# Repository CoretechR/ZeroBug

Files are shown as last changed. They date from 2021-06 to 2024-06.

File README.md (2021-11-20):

# ZeroBug - DIY Hexapod Robot

Zerobug is a 3D-printed micro-servo hexapod robot powered by a Raspberry Pi Zero and a STM32F103. The Pi Zero is in charge of the input methods and front end, making the robot controllable via mouse, keyboard, multitouch or simply a Bluetooth Gamepad. To get the robot walking, the STM32 handles leg locomotion, inverse kinematics and controls its 18 servos.

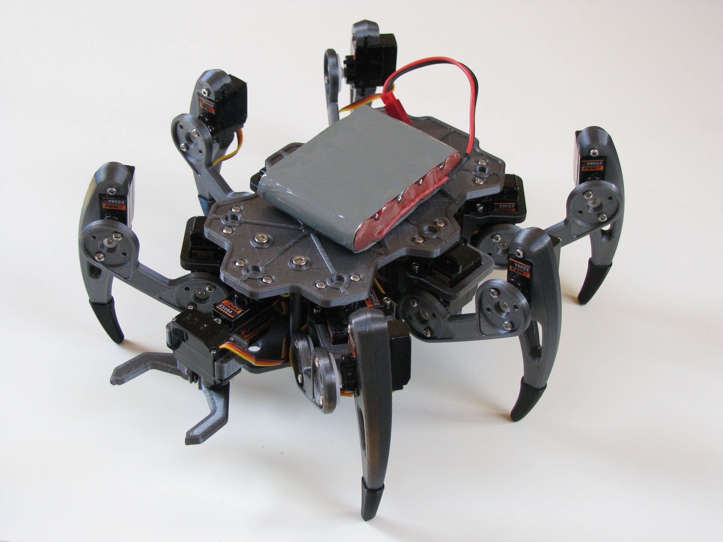
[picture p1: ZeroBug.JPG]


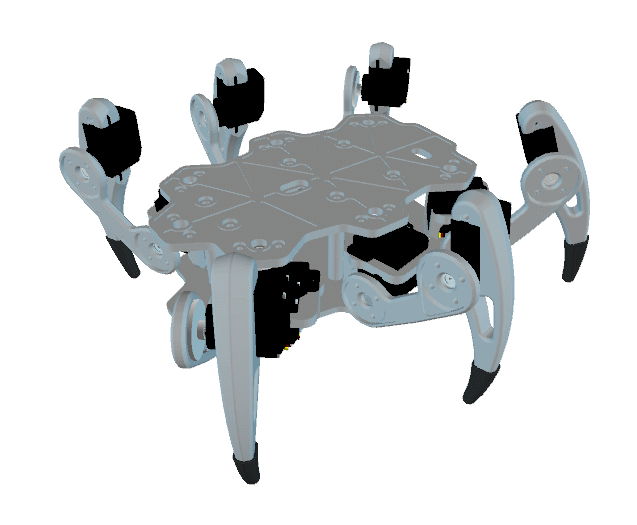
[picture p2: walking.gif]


UPDATE 20.11.2021: Added support for video streaming with via the camera connector:
 - update the index-html file and copy "start_stream.sh" to the same directory on the desktop
 - install mjpg-streamer (e.g. using this guide: https://www.okdo.com/project/pc-webcam-with-raspberry-pi/?ok_ts=1635608250445)
 - add the following line to the /etc/rc.local file (before exit 0):
```
bash /home/pi/Desktop/hexapod/start_stream.sh
```

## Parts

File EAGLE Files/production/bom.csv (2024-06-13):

Designator | Footprint | Quantity | Value | LCSC Part #
@HOLE0, @HOLE1, @HOLE10, @HOLE11, @HOLE12, @HOLE13, @HOLE2, @HOLE3, @HOLE4, @HOLE5, @HOLE6, @HOLE7, @HOLE8, @HOLE9 |  | 14
C1 | 0805 | 1 | 10uF
C10, C11, C14, C15, C2, C8 | 0805 | 6 | 1.0uF
C12, C13 | 0603 | 2 | 47pF
C17 | 0603 | 1 | 10nF
C18, C9 | 0805 | 2 | 2.2uF
C20, C21 | 0603 | 2 | 0.1uF
C3 | 0805 | 1 | 4.7uF
C5 | PANASONIC_D | 1 | 100uF
C6, C7 | 0603 | 2 | 18pF
CN1 | 1X04-BIG | 1 | 1X4-BIG
D1, D3 | SOD-323 | 2 | BAT20J
D2 | LED-0603@2 | 1 | BLUE
F1 | PTC-1206 | 1 | 500mA
J1 | TERMBLOCK_1X2-3.5MM | 1
J10, J11, J12, J13, J14, J15, J16, J17, J18, J19, J20, J21, J22, J3, J4, J5, J6, J7, J8, J9 | 1X03 | 20
J2 | USB-C-16P | 1
J23 | 61031021821 | 1
OSC0 | CRYSTAL-SMD-5X3 | 1 | 8MHz
Q1 | TO252 | 1 | AOD417
R1, R2 | 0603 | 2 | 0
R12, R15, R4, R6, R7, R8 | 0603 | 6 | 10k
R13, R14 | 0603 | 2 | 27
R16, R17, R18, R9 | 0603 | 4 | 1k
R19, R3 | 0603 | 2 | 5.1k
R20 | 0603 | 1 | 1k5
R5 | 0603 | 1 | 4.7k
S1 | TACTILE_SWITCH_SMD_4.6X2.8MM | 1 | RESET
SJ1, SJ2 | PAD-JUMPER-2-NO_YES_SILK | 2
U$2 | QFN-24-4MM2 | 1 | MPU-6050-1
U2 | TSSOP28 | 1
U3 | SOT23-5 | 1 | AP2112K-3.3V
U4 | SOT230P700X180-4N | 1 | MCP1825S-5002E/DB
UC1 | LQFP48 | 1 | STM32F103CBT6

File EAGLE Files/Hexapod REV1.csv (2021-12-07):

Qty | Value | Device | Package | Parts | Description | DATASHEET-URL | GENDER | IR | MPN | OC_FARNELL | OC_NEWARK | PACKAGE | PACKAGING | PART-NUMBER | PINS | PROD_ID | ROWS | SUPPLIER | TYPE | VALUE | WE-NUMBER
1 |  | 6103XX21821_61031021821 | 61031021821 | J23 | WR-PHD 2.54 mm SMT Dual Socket Header (Reel) | https://katalog.we-online.com/em/datasheet/61031021821.pdf | Socket Header | 3A |  |  |  |  | Tape and Reel with Cap | 61031021821 | 10 |  | Dual |  | Straight Type 2 |  | 61031021821
20 |  | CONN_03 | 1X03 | J3; J4; J5; J6; J7; J8; J9; J10; J11; J12; J13; J14; J15; J16; J17; J18; J19; J20; J21; J22 | Multi connection point. Often used as Generic Header-pin footprint for 0.1 inch spaced/style header connections |  |  |  |  |  |  |  |  |  |  | XXX-00000 |  |  |  | 455-1750-1-ND
2 |  | JUMPER-PAD-2-NOYES_SILK | PAD-JUMPER-2-NO_YES_SILK | SJ1; SJ2
1 |  | PCA9685 | TSSOP28 | U2 | PCA9685 - 16 Channel 12-Bit I2C PWM Controller
1 |  | TERMBLOCK_1X2 | TERMBLOCK_1X2-3.5MM | J1 | 3.5mm Terminal block
1 |  | USB_C16PIN | USB-C-16P | J2 | USB Type C 16Pin Connector |  |  |  |  |  |  |  |  |  |  | CONN-14122
2 | 0 | 10KOHM-0603-1/10W-1% | 0603 | R1; R2 | 10kO resistor |  |  |  |  |  |  |  |  |  |  | RES-00824 |  |  |  | 10k
2 | 0.1uF | 0.1UF-0603-25V-(+80/-20%) | 0603 | C20; C21 | 0.1µF ceramic capacitors |  |  |  |  |  |  |  |  |  |  | CAP-00810 |  |  |  | 0.1uF
6 | 1.0uF | 1.0UF-0805-25V-(+80/-20%) | 0805 | C2; C8; C10; C11; C14; C15 | 1µF ceramic capacitors |  |  |  |  |  |  |  |  |  |  | CAP-11625 |  |  |  | 1.0uF
1 | 100uF | 100UF-POLAR-25V-20%(ELEC) | PANASONIC_D | C5 | 100µF polarized capacitors |  |  |  |  |  |  |  |  |  |  | CAP-12547 |  |  |  | 100uF
6 | 10k | 10KOHM-0603-1/10W-1% | 0603 | R4; R6; R7; R8; R12; R15 | 10kO resistor |  |  |  |  |  |  |  |  |  |  | RES-00824 |  |  |  | 10k
1 | 10nF | 47PF-0603-50V-5% | 0603 | C17 | 47pF ceramic capacitors |  |  |  |  |  |  |  |  |  |  | CAP-08913 |  |  |  | 47pF
1 | 10uF | 1.0UF-0805-25V-(+80/-20%) | 0805 | C1 | 1µF ceramic capacitors |  |  |  |  |  |  |  |  |  |  | CAP-11625 |  |  |  | 1.0uF
2 | 18pF | 47PF-0603-50V-5% | 0603 | C6; C7 | 47pF ceramic capacitors |  |  |  |  |  |  |  |  |  |  | CAP-08913 |  |  |  | 47pF
1 | 1X4-BIG | 1X4-BIG | 1X04-BIG | CN1 | 4-pin connector
3 | 1k | 10KOHM-0603-1/10W-1% | 0603 | R16; R17; R18 | 10kO resistor |  |  |  |  |  |  |  |  |  |  | RES-00824 |  |  |  | 10k
1 | 1k | 1KOHM-0603-1/10W-1% | 0603 | R9 | 1kO resistor |  |  |  |  |  |  |  |  |  |  | RES-07856 |  |  |  | 1k
1 | 1k5 | 10KOHM-0603-1/10W-1% | 0603 | R20 | 10kO resistor |  |  |  |  |  |  |  |  |  |  | RES-00824 |  |  |  | 10k
2 | 2.2uF | 1.0UF-0805-25V-(+80/-20%) | 0805 | C9; C18 | 1µF ceramic capacitors |  |  |  |  |  |  |  |  |  |  | CAP-11625 |  |  |  | 1.0uF
2 | 27 | 27OHM1/10W1%(0603)0603-RES | 0603 | R13; R14 | RES-09334 |  |  |  |  |  |  |  |  |  |  | RES-09334
1 | 4.7k | 10KOHM-0603-1/10W-1% | 0603 | R5 | 10kO resistor |  |  |  |  |  |  |  |  |  |  | RES-00824 |  |  |  | 10k
1 | 4.7uF | 1.0UF-0805-25V-(+80/-20%) | 0805 | C3 | 1µF ceramic capacitors |  |  |  |  |  |  |  |  |  |  | CAP-11625 |  |  |  | 1.0uF
2 | 47pF | 47PF-0603-50V-5% | 0603 | C12; C13 | 47pF ceramic capacitors |  |  |  |  |  |  |  |  |  |  | CAP-08913 |  |  |  | 47pF
2 | 5.1k | 10KOHM-0603-1/10W-1% | 0603 | R3; R19 | 10kO resistor |  |  |  |  |  |  |  |  |  |  | RES-00824 |  |  |  | 10k
1 | 500mA | PTCSMD | PTC-1206 | F1 | Resettable Fuse PTC |  |  |  |  |  |  |  |  |  |  | RES-11150
1 | 8MHz | CRYSTAL5X3 | CRYSTAL-SMD-5X3 | OSC | Crystals
1 | AOD417 | MOSFET-PTO252 | TO252 | Q1 | P-Channel Mosfet
1 | AP2112K-3.3V | V_REG_LDOSMD | SOT23-5 | U3 | Voltage Regulator LDO |  |  |  |  |  |  |  |  |  |  | VREG-12457
2 | BAT20J | DIODE-SCHOTTKY-BAT20J | SOD-323 | D1; D3 | Schottky diodes in SFE's production catalog |  |  |  |  |  |  |  |  |  |  | DIO-11623 |  |  |  | BAT20J
1 | BLUE | LED-BLUE0603 | LED-0603@2 | D2 | Blue SMD LED |  |  |  |  |  |  |  |  |  |  | DIO-08575 |  |  |  | BLUE
1 | MCP1825S-5002E/DB | MCP1825S-5002E/DB | SOT230P700X180-4N | U4 | IC; LDO; 5.0V; 500MA |  |  |  | MCP1825S-5002E/DB | 1578407 | 26M9964 | SOT-223-3 |  |  |  |  |  | Microchip
1 | MPU-6050-1 | MPU-6050-1 | QFN-24-4MM2 | U$2
1 | RESET | MOMENTARY-SWITCH-SPST-2-SMD-4.6X2.8MM | TACTILE_SWITCH_SMD_4.6X2.8MM | S1 | Momentary Switch (Pushbutton) - SPST - Two Circuits |  |  |  |  |  |  |  |  |  |  | SWCH-13065
1 | STM32F103CBT6 | STM32F103CB | LQFP48 | UC1

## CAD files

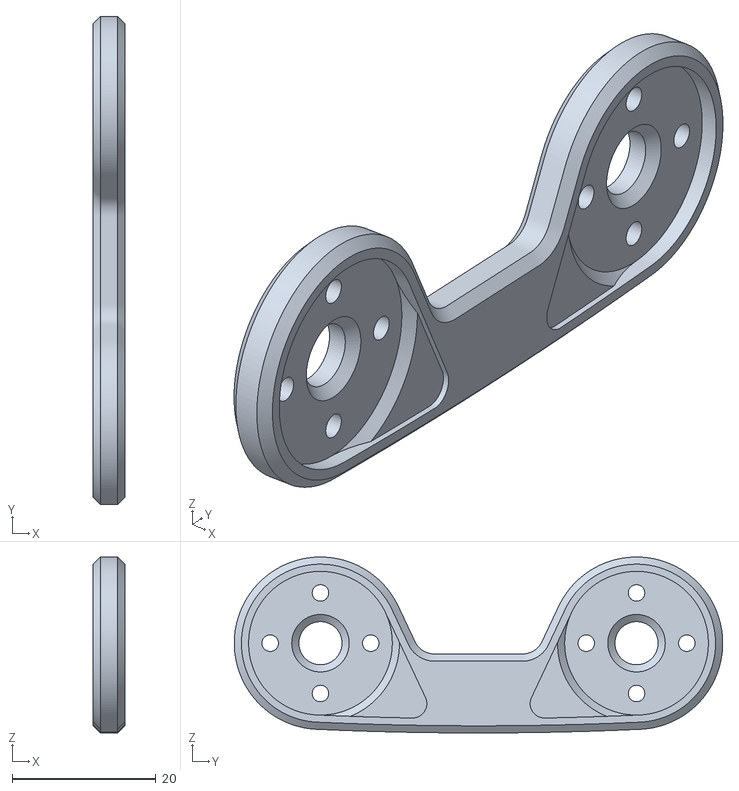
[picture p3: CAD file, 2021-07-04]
CAD Files/femur.stl
4.40 x 68.0 x 24.5

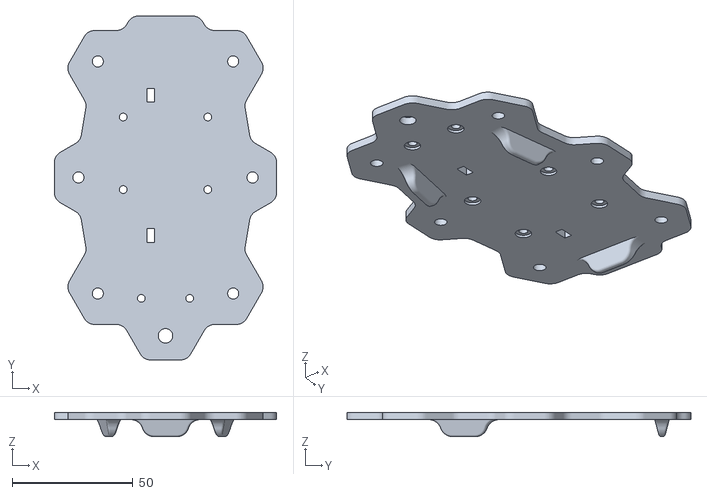
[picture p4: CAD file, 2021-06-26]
CAD Files/Body Bot.stl
92.0 x 142.3 x 10.0

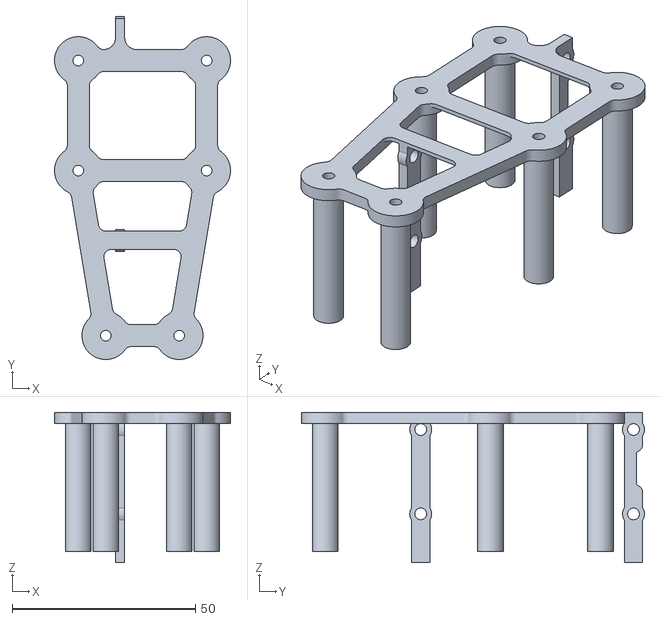
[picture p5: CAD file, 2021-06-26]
CAD Files/Spacer.stl
48.0 x 93.5 x 41.0

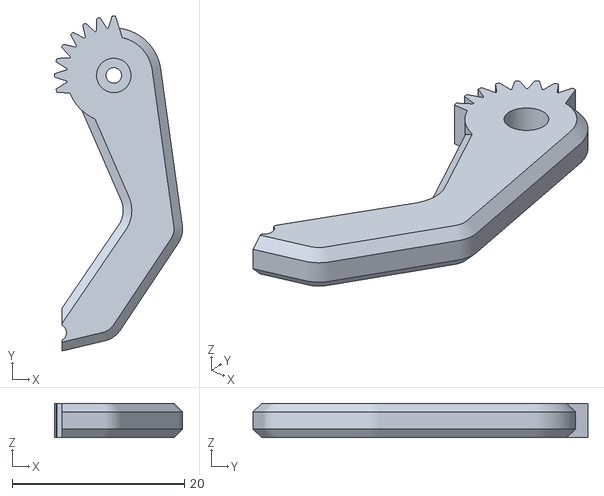
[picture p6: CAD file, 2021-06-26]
CAD Files/gripper_clawL.stl
14.9 x 38.9 x 4.00

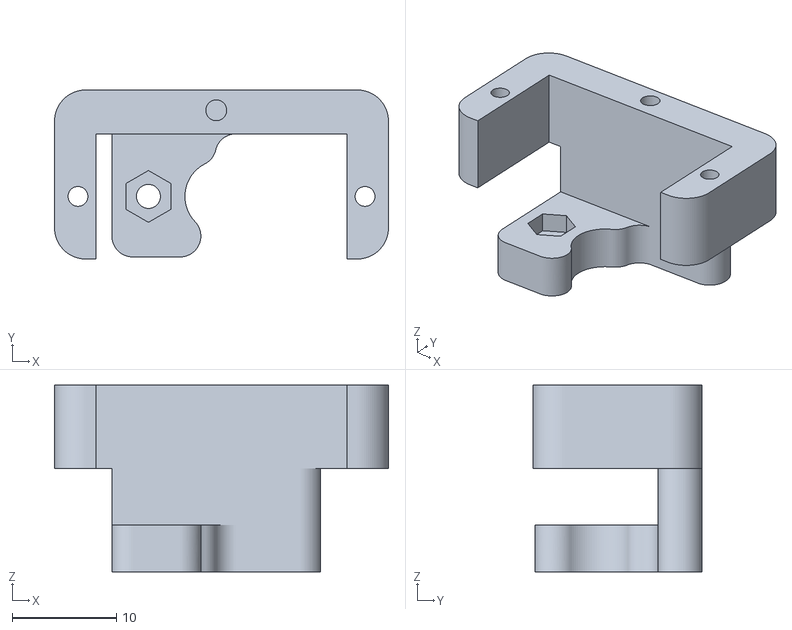
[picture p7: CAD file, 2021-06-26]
CAD Files/gripper_body.stl
32.0 x 16.2 x 17.9

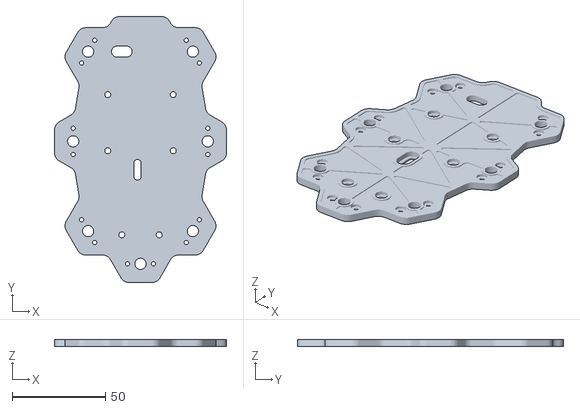
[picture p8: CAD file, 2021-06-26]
CAD Files/Body Top.stl
92.0 x 142.3 x 3.60

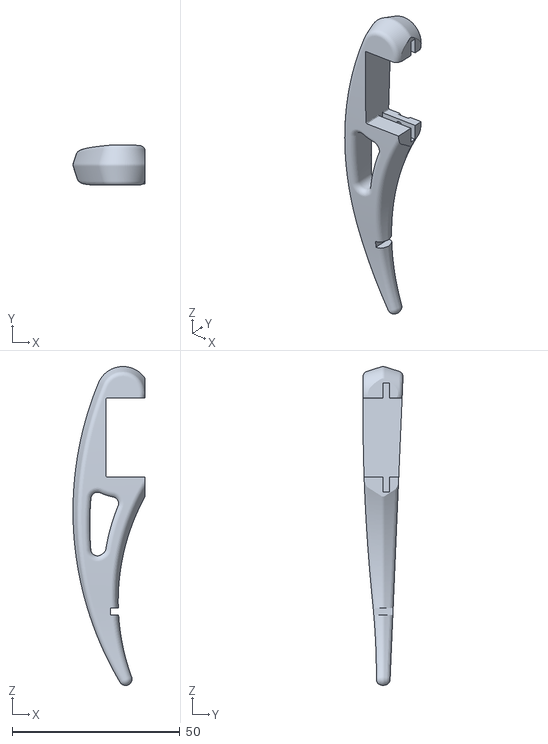
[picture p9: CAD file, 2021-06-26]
CAD Files/Tibia.stl
21.5 x 11.9 x 95.1

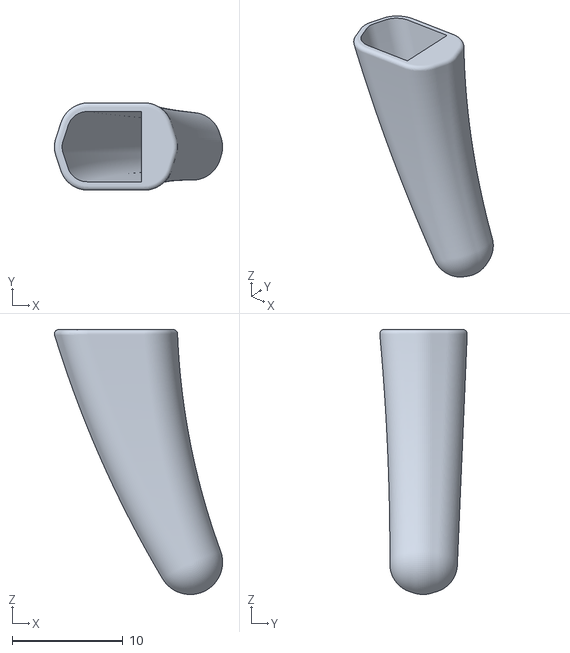
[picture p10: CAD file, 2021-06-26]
CAD Files/Sock.stl
15.2 x 7.89 x 23.9

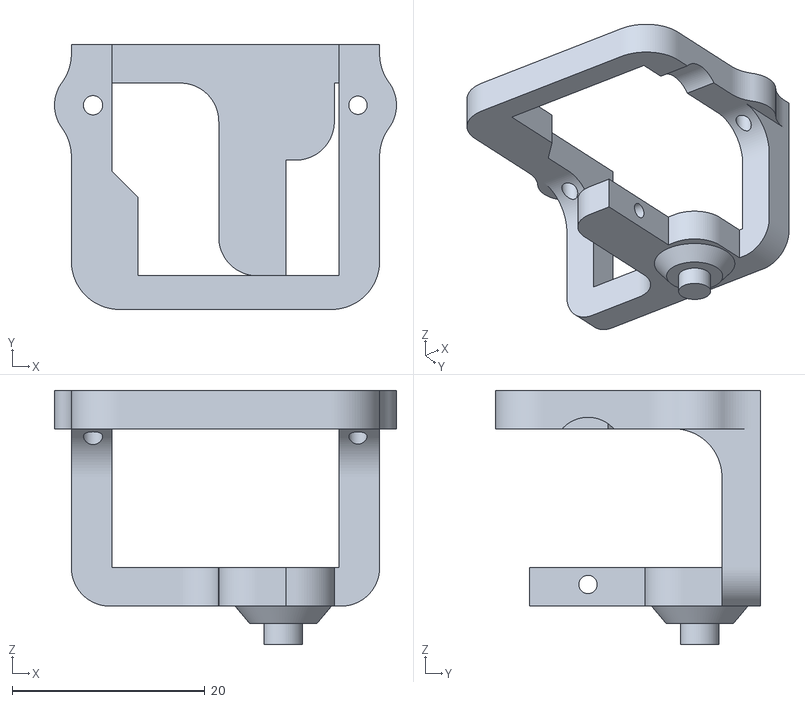
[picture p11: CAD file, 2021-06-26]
CAD Files/Coxa.stl
35.5 x 27.5 x 26.4

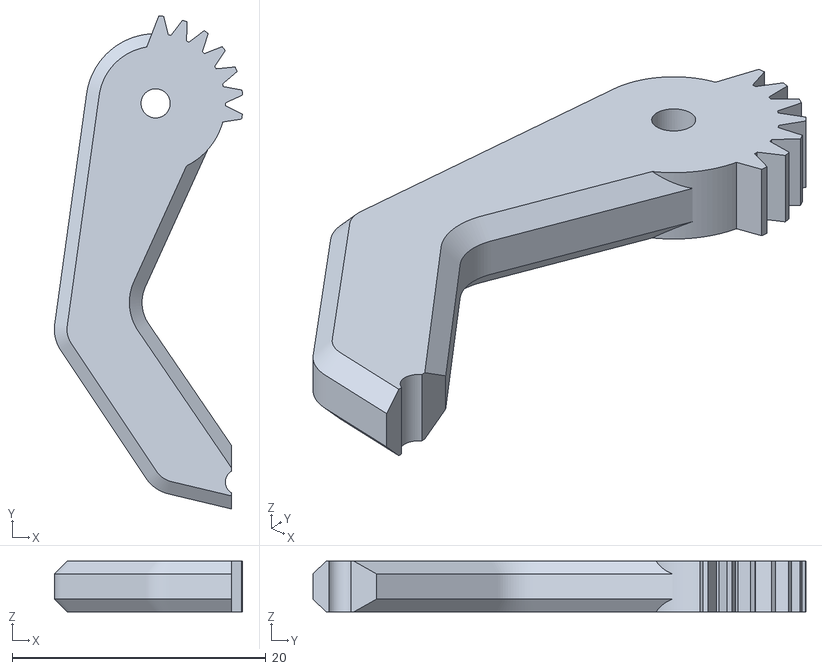
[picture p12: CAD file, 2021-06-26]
CAD Files/gripper_clawR.stl
14.9 x 38.9 x 4.00

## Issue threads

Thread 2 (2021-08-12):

miss file for CAD File

nongxiaoming, 2021-08-12:
hi，also miss some file for CAD File. no have the CoxaM.stl and TibiaM.stl??

CoretechR, 2021-08-12:
Hi, those are just the mirrored variants. Your slicer software should have an option to flip the parts. If not I can upload them as well.

nongxiaoming, 2021-08-19:
Ok,Got it.Thanks

Closed 2021-08-19.

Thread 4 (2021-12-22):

Raspberry PI software does not work

kenking2536, 2021-12-22:
Raspberry PI software does not work

I'm not familiar with Raspberry PI. Please guide me how to install it,

Copy what files to where??

What documents and contents are modified??

I'm using Raspberry PI zero 2 W

Not Raspberry PI zero w

kenking2536, 2021-12-25:
After many days of hard work! Learned a lot of knowledge! Finally, this problem occurs! Please have a look!
My zero 2 W installation process is as follows:

sudo apt-get install subversion
sudo apt-get install imagemagick
sudo apt-get install cmake
sudo apt-get install git
sudo apt-get install libv4l-dev
sudo apt-get install libopencv-dev
sudo apt-get install gcc g++
sudo apt-get install libjpeg9-dev
sudo apt-get install libjpeg62-turbo-dev
sudo apt-get install xrdp
sudo apt-get install samba
sudo apt-get install nodejs
sudo apt-get install npm
npm install socket.io
pip3 install aiohttp
pip3 install aiodns
pip3 install cchardet
pip3 install asyncio
pip3 install pygame
sudo git clone https://github.com/jacksonliam/mjpg-streamer
cd mjpg-streamer/mjpg-streamer-experimental
sudo make all
sudo make install
/home/pi/mjpg-streamer/mjpg-streamer-experimental/./mjpg_streamer -i "input_raspicam.so -x 1280 -y 720 -fps 12" -o "output_http.so -w ./www"
sudo cp mjpg_streamer@.service /etc/systemd/system
cd /etc/systemd/system
sudo mv mjpg_streamer@.service mjpg_streamer.service
sudo nano /etc/systemd/system/mjpg_streamer.service
sudo systemctl start mjpg_streamer.service
sudo systemctl enable mjpg_streamer.service
vcgencmd get_camera

Finally, the following error is displayed:
Traceback (most recent call last):
  File "/home/pi/ZeroBug/app.py", line 2, in <module>
    import socketio
ModuleNotFoundError: No module named 'socketio'

Closed 2021-12-25.

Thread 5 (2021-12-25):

Raspberry PI software does not work

kenking2536, 2021-12-25:
Raspberry PI software does not work

I'm not familiar with Raspberry PI. Please guide me how to install it,

Copy what files to where??

What documents and contents are modified??

I'm using Raspberry PI zero 2 W

Not Raspberry PI zero w

After many days of hard work! Learned a lot of knowledge! Finally, this problem occurs! Please have a look!
My zero 2 W installation process is as follows:

sudo apt-get install subversion
sudo apt-get install imagemagick
sudo apt-get install cmake
sudo apt-get install git
sudo apt-get install libv4l-dev
sudo apt-get install libopencv-dev
sudo apt-get install gcc g++
sudo apt-get install libjpeg9-dev
sudo apt-get install libjpeg62-turbo-dev
sudo apt-get install xrdp
sudo apt-get install samba
sudo apt-get install nodejs
sudo apt-get install npm
npm install socket.io
pip3 install aiohttp
pip3 install aiodns
pip3 install cchardet
pip3 install asyncio
pip3 install pygame
sudo git clone https://github.com/jacksonliam/mjpg-streamer
cd mjpg-streamer/mjpg-streamer-experimental
sudo make all
sudo make install
/home/pi/mjpg-streamer/mjpg-streamer-experimental/./mjpg_streamer -i "input_raspicam.so -x 1280 -y 720 -fps 12" -o "output_http.so -w ./www"
sudo cp mjpg_streamer@.service /etc/systemd/system
cd /etc/systemd/system
sudo mv mjpg_streamer@.service mjpg_streamer.service
sudo nano /etc/systemd/system/mjpg_streamer.service
sudo systemctl start mjpg_streamer.service
sudo systemctl enable mjpg_streamer.service
vcgencmd get_camera

Finally, the following error is displayed:
Traceback (most recent call last):
File "/home/pi/ZeroBug/app.py", line 2, in
import socketio
ModuleNotFoundError: No module named 'socketio'

pageauc, 2021-12-25:
You might try

sudo apt install socket.io

rather than rpm install

On Fri, Dec 24, 2021 at 8:41 PM kenking2536 ***@***.***>
wrote:

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

--
YouTube Channel at https://www.youtube.com/user/pageaucp
<http://www.youtube.com/user/pageaucp>
GitHub Repository at https://github.com/pageauc

kenking2536, 2021-12-25:
socket. IO problem solved!

thank!

Universal sudo apt-get install

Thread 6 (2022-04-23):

STM32F103C8T6

debian-user-france1, 2022-04-23:
The STM32F103C8T6 is not available anymore, what can I buy instead without reprogramming or much trouble?

debian-user-france1, 2022-04-23:
EMAX ES08A II Micro Servos are sold out, too

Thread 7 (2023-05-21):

Is the mpu 6050 used?

renhang123, 2023-05-21:
Hi, I looked at your source code and I can't seem to find the code for reading mpu 6050 data. Could you tell me where the data of mpu 6050 is used?

CoretechR, 2023-05-21:
Hi, the MPU6050 was never used on this board. I was planning to use it for balancing and still has some room on the PCB but never got around to implement it.

Closed 2023-05-22.

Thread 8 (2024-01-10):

Programming the STM32

weizhuowang, 2024-01-10:
Thanks for open sourcing the project! I see that the STM32F103 is using Arduino code. I wonder what is the best way to send the bootloader to mcu so that it accepts flashes from USB port?

CoretechR, 2024-01-10:
Hi, I wrote some instruction for another project that uses the STM32F103: https://github.com/CoretechR/Keybon
Maybe this will help you already.

Closed 2024-01-10.

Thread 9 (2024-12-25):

Servo Motor Replacement: EMAX ES08A II vs. Tower Pro MG90S

BiyolojiMeb, 2024-12-25:
Hello,
I can't find the EMAX ES08A II servo motor. Would it be okay if I use the Tower Pro MG90S instead?
Thanks!

CoretechR, 2024-12-25:
Hi, you should be able to use any micro servo, but you have to check the exact dimensions. The 3D-printed parts and especially the screw holes will probably not fit without some modifications.
Generally, I would recommend using the ES08A or a higher quality servo. The MG90S are not as fast and precise as the ES08A.

tianyi725, 2024-12-28:
> Hi, you should be able to use any micro servo, but you have to check the exact dimensions. The 3D-printed parts and especially the screw holes will probably not fit without some modifications. Generally, I would recommend using the ES08A or a higher quality servo. The MG90S are not as fast and precise as the ES08A.

thankyou

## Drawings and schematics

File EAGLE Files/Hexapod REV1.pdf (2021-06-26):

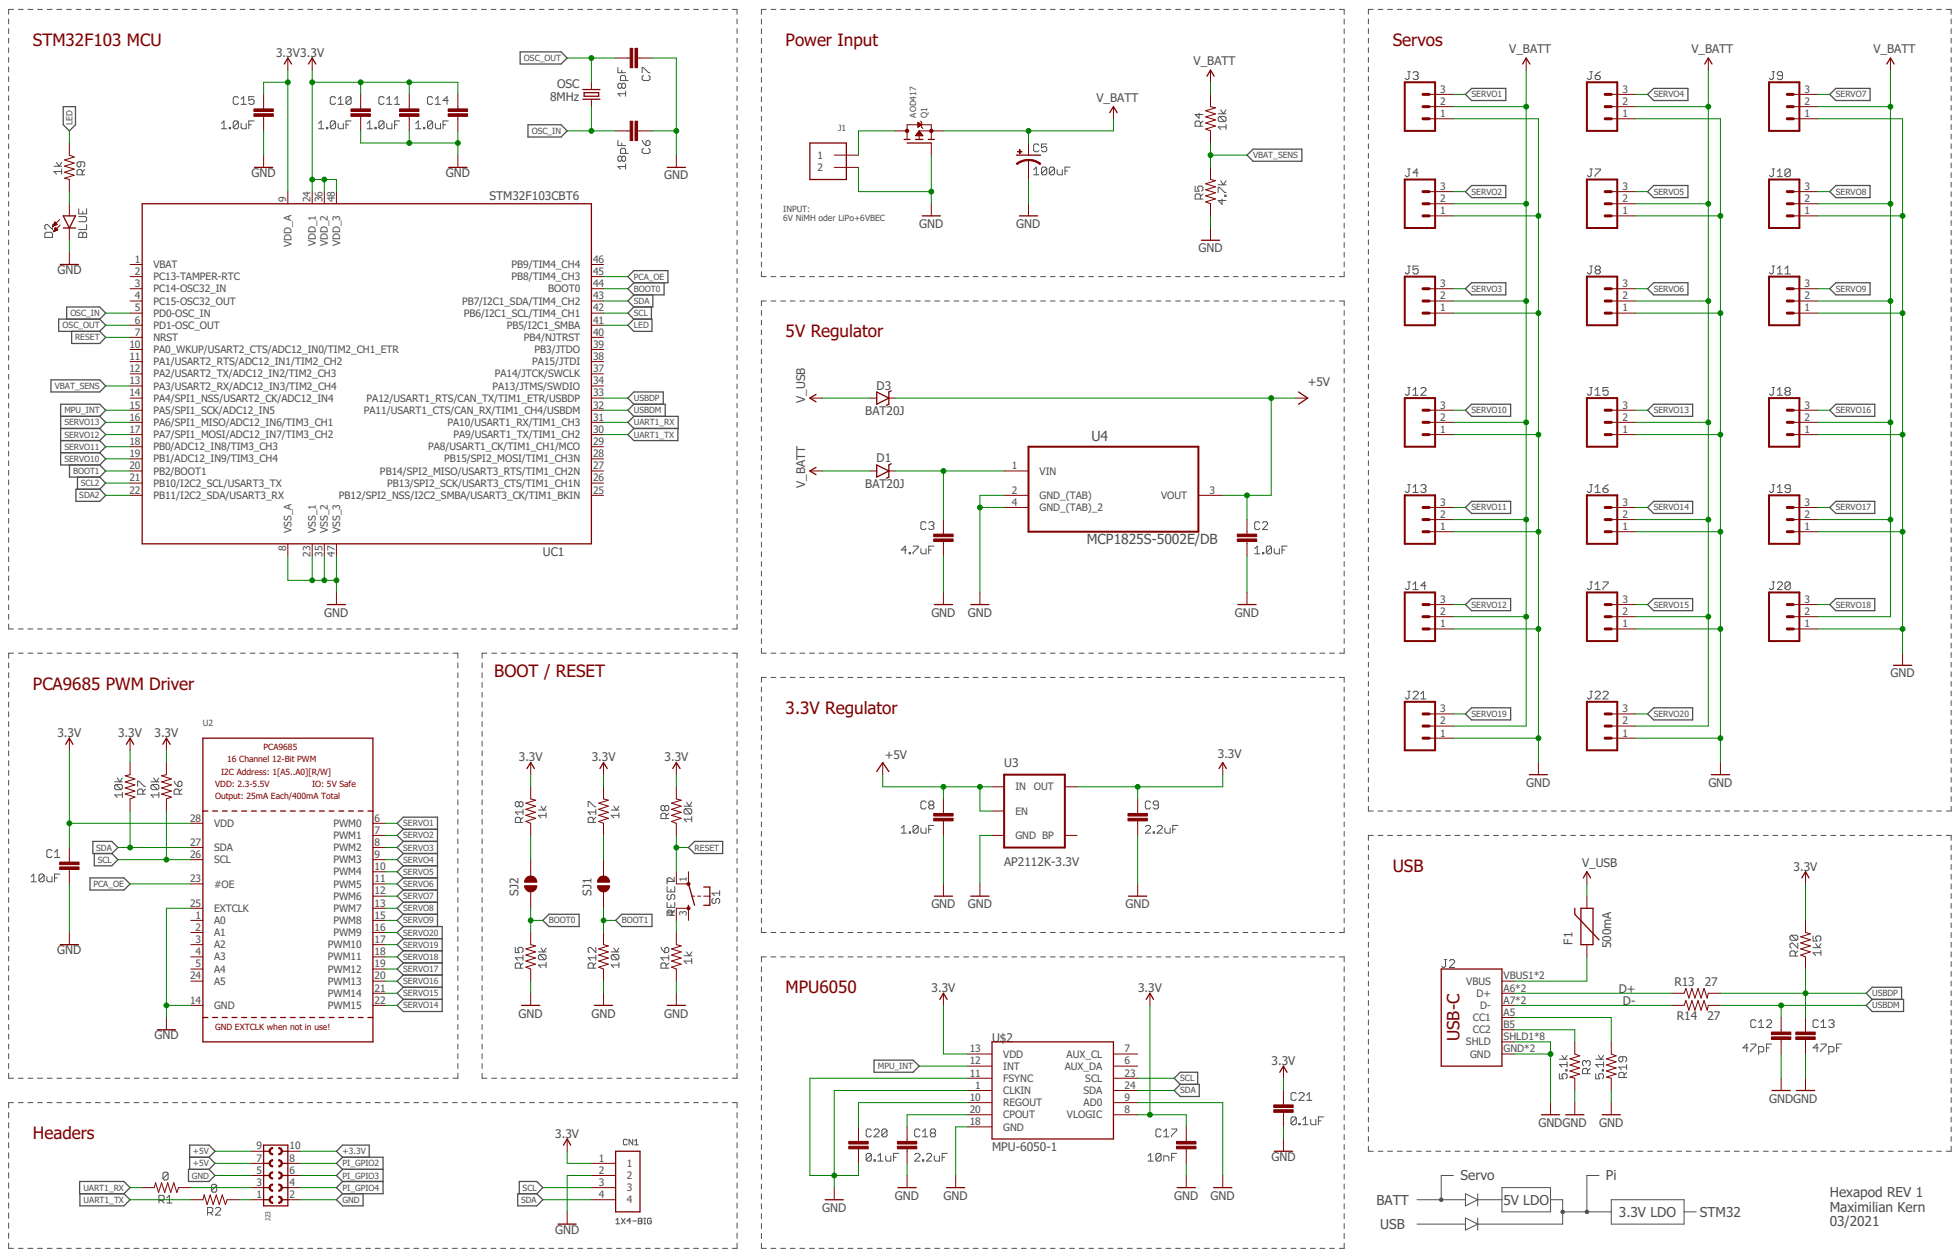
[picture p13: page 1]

INPUT: 6V NiMH oder LiPo+6VBEC

GND EXTCLK when not in use!

Hexapod REV 1 Maximilian Kern

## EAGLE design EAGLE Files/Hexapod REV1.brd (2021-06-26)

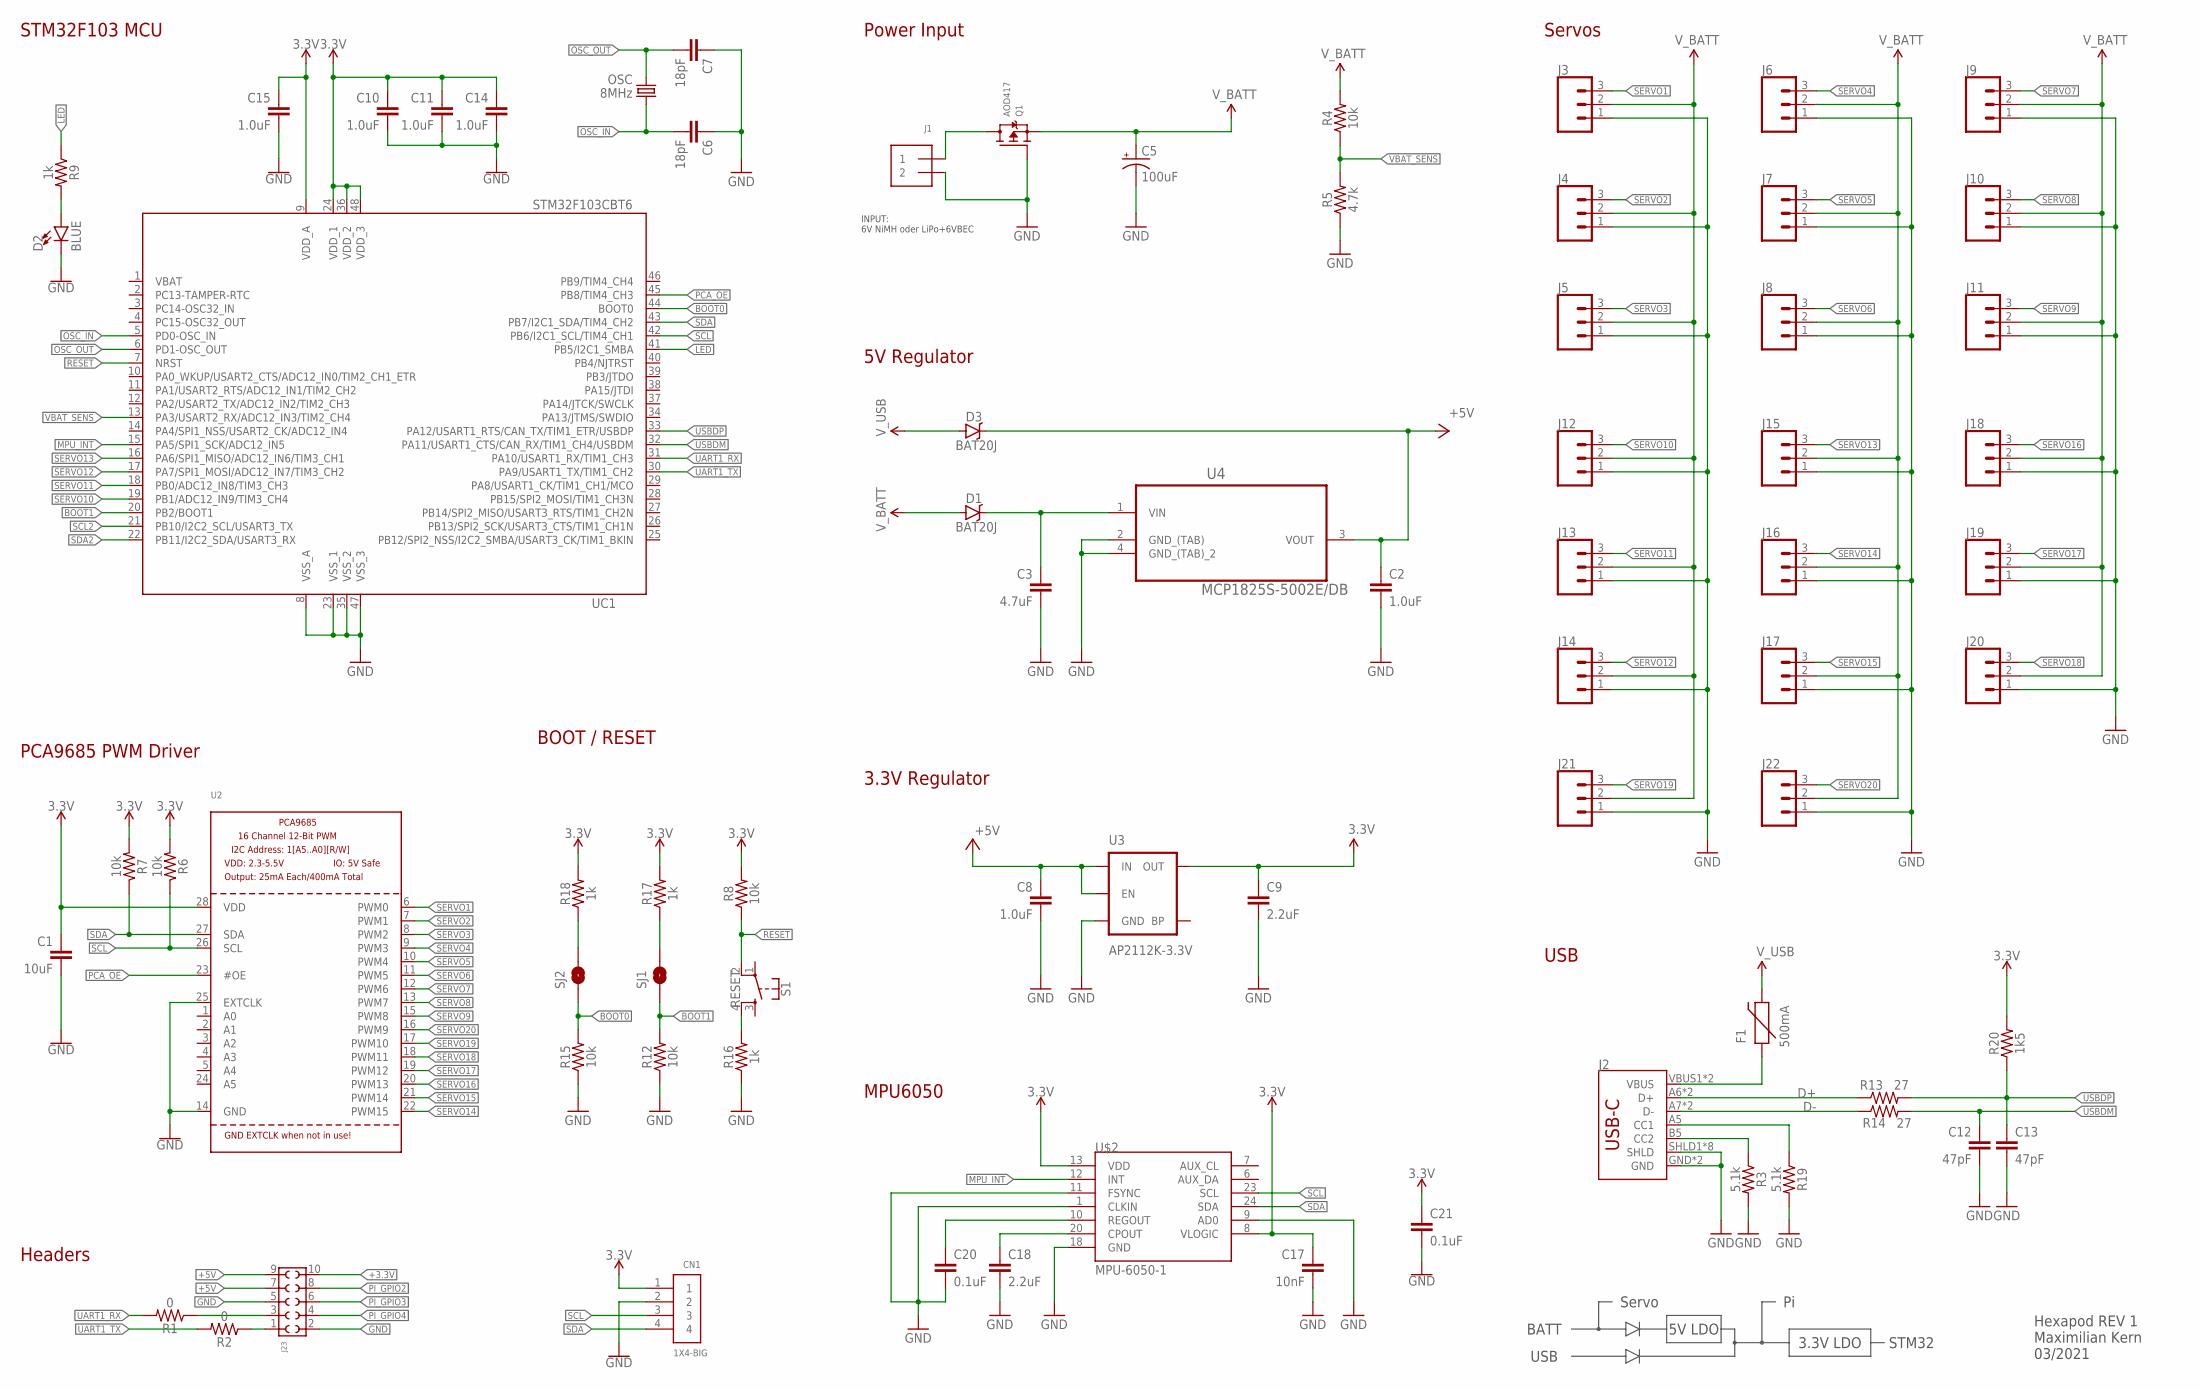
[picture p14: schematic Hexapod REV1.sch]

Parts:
C1: 10uF; 0805
C2, C8, C10, C11, C14, C15: 1.0uF; 0805
C3: 4.7uF; 0805
C5: 100uF; PANASONIC_D
C6, C7: 18pF; 0603
C9, C18: 2.2uF; 0805
C12, C13: 47pF; 0603
C17: 10nF; 0603
C20, C21: 0.1uF; 0603
CN1: 1X4-BIG; 1X04-BIG
D1, D3: BAT20J; SOD-323
D2: BLUE; LED-0603@2
F1: 500mA; PTC-1206
J1: TERMBLOCK_1X2; TERMBLOCK_1X2-3.5MM
J2: USB_C16PIN; USB-C-16P
J3, J4, J5, J6, J7, J8, J9, J10, J11, J12, J13, J14, J15, J16, J17, J18, J19, J20, J21, J22: CONN_03; 1X03
J23: 6103XX21821_61031021821; 61031021821
OSC: 8MHz; CRYSTAL-SMD-5X3
Q1: AOD417; TO252
R1, R2: 0; 0603
R3, R19: 5.1k; 0603
R4, R6, R7, R8, R12, R15: 10k; 0603
R5: 4.7k; 0603
R9, R16, R17, R18: 1k; 0603
R13, R14: 27; 0603
R20: 1k5; 0603
S1: RESET; TACTILE_SWITCH_SMD_4.6X2.8MM
SJ1, SJ2: JUMPER-PAD-2-NOYES_SILK; PAD-JUMPER-2-NO_YES_SILK
U2: PCA9685; TSSOP28
U3: AP2112K-3.3V; SOT23-5
U4: MCP1825S-5002E/DB; SOT230P700X180-4N
U$2: MPU-6050-1; QFN-24-4MM2
UC1: STM32F103CBT6; LQFP48

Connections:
3.3V: C1.1, C9.1, C10.1, C11.1, C14.1, C15.1, C17.1, C21.1, CN1.1, R6.2, R7.2, R8.2, R17.2, R18.2, R20.2, U2.28 (VDD), U3.5 (OUT), U$2.8 (VLOGIC), U$2.13 (VDD), UC1.9 (VDD_A), UC1.24 (VDD_1), UC1.36 (VDD_2), UC1.48 (VDD_3)
+3.3V: J23.10
+5V: C2.1, C8.1, D3.C, J23.7, J23.9, U3.1 (IN), U3.3 (EN), U4.3 (VOUT)
BOOT0: R15.2, SJ2.1, UC1.44 (BOOT0)
BOOT1: R12.2, SJ1.1, UC1.20 (PB2/BOOT1)
D+: J2.A6 (D+), J2.B6 (D+), R13.1
D-: J2.A7 (D-), J2.B7 (D-), R14.1
GND: C1.2, C2.2, C3.2, C5.-, C6.1, C7.1, C8.2, C9.2, C10.2, C11.2, C12.2, C13.2, C14.2, C15.2, C17.2, C18.2, C20.2, C21.2, CN1.2, D2.C, J1.2, J2.GND, J2.GND2 (GND), J2.SHLD1 (SHLD), J2.SHLD2 (SHLD), J2.SHLD3 (SHLD), J2.SHLD4 (SHLD), J2.SHLD5 (SHLD), J2.SHLD6 (SHLD), J2.SHLD7 (SHLD), J2.SHLD8 (SHLD), J3.1, J4.1, J5.1, J6.1, J7.1, J8.1, J9.1, J10.1, J11.1, J12.1, J13.1, J14.1, J15.1, J16.1, J17.1, J18.1, J19.1, J20.1, J21.1, J22.1, J23.2, J23.5, Q1.1 (G), R3.2, R5.1, R12.1, R15.1, R16.1, R19.2, U2.14 (GND), U2.25 (EXTCLK), U3.2 (GND), U4.2 (GND_(TAB)), U4.4 (GND_(TAB)_2), U$2.1 (CLKIN), U$2.9 (AD0), U$2.11 (FSYNC), U$2.18 (GND), UC1.8 (VSS_A), UC1.23 (VSS_1), UC1.35 (VSS_2), UC1.47 (VSS_3)
LED: R9.1, UC1.41 (PB5/I2C1_SMBA)
MPU_INT: U$2.12 (INT), UC1.15 (PA5/SPI1_SCK/ADC12_IN5)
unnamed: R16.2, S1.4
unnamed: R18.1, SJ2.2
unnamed: R17.1, SJ1.2
unnamed: C3.1, D1.C, U4.1 (VIN)
unnamed: D2.A, R9.2
unnamed: J1.1, Q1.3 (D)
unnamed: J2.A5 (CC1), R19.1
unnamed: J2.B5 (CC2), R3.1
unnamed: C18.1, U$2.20 (CPOUT)
unnamed: C20.1, U$2.10 (REGOUT)
OSC_IN: C6.2, OSC.1, UC1.5 (PD0-OSC_IN)
OSC_OUT: C7.2, OSC.3 (2), UC1.6 (PD1-OSC_OUT)
PCA_OE: U2.23 (#OE), UC1.45 (PB8/TIM4_CH3)
PI_GPIO2: J23.8
PI_GPIO3: J23.6
PI_GPIO4: J23.4
PI_RXD: J23.1, R2.1
PI_TXD: J23.3, R1.1
RESET: R8.1, S1.2, UC1.7 (NRST)
SCL: CN1.3, R6.1, U2.26 (SCL), U$2.23 (SCL), UC1.42 (PB6/I2C1_SCL/TIM4_CH1)
SCL2: UC1.21 (PB10/I2C2_SCL/USART3_TX)
SDA: CN1.4, R7.1, U2.27 (SDA), U$2.24 (SDA), UC1.43 (PB7/I2C1_SDA/TIM4_CH2)
SDA2: UC1.22 (PB11/I2C2_SDA/USART3_RX)
SERVO1: J3.3, U2.6 (PWM0)
SERVO2: J4.3, U2.7 (PWM1)
SERVO3: J5.3, U2.8 (PWM2)
SERVO4: J6.3, U2.9 (PWM3)
SERVO5: J7.3, U2.10 (PWM4)
SERVO6: J8.3, U2.11 (PWM5)
SERVO7: J9.3, U2.12 (PWM6)
SERVO8: J10.3, U2.13 (PWM7)
SERVO9: J11.3, U2.15 (PWM8)
SERVO10: J12.3, UC1.19 (PB1/ADC12_IN9/TIM3_CH4)
SERVO11: J13.3, UC1.18 (PB0/ADC12_IN8/TIM3_CH3)
SERVO12: J14.3, UC1.17 (PA7/SPI1_MOSI/ADC12_IN7/TIM3_CH2)
SERVO13: J15.3, UC1.16 (PA6/SPI1_MISO/ADC12_IN6/TIM3_CH1)
SERVO14: J16.3, U2.22 (PWM15)
SERVO15: J17.3, U2.21 (PWM14)
SERVO16: J18.3, U2.20 (PWM13)
SERVO17: J19.3, U2.19 (PWM12)
SERVO18: J20.3, U2.18 (PWM11)
SERVO19: J21.3, U2.17 (PWM10)
SERVO20: J22.3, U2.16 (PWM9)
UART1_RX: R1.2, UC1.31 (PA10/USART1_RX/TIM1_CH3)
UART1_TX: R2.2, UC1.30 (PA9/USART1_TX/TIM1_CH2)
USBDM: C12.1, R14.2, UC1.32 (PA11/USART1_CTS/CAN_RX/TIM1_CH4/USBDM)
USBDP: C13.1, R13.2, R20.1, UC1.33 (PA12/USART1_RTS/CAN_TX/TIM1_ETR/USBDP)
VBAT: UC1.1 (VBAT)
VBAT_SENS: R4.1, R5.2, UC1.13 (PA3/USART2_RX/ADC12_IN3/TIM2_CH4)
VUSB-RAW: F1.1, J2.VBUS1 (VBUS), J2.VBUS2 (VBUS)
V_BATT: C5.+, D1.A, J3.2, J4.2, J5.2, J6.2, J7.2, J8.2, J9.2, J10.2, J11.2, J12.2, J13.2, J14.2, J15.2, J16.2, J17.2, J18.2, J19.2, J20.2, J21.2, J22.2, Q1.2 (S), R4.2
V_USB: D3.A, F1.2

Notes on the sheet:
STM32F103 MCU
USB
BOOT / RESET
3.3V Regulator
Hexapod REV 1 Maximilian Kern 03/2021
INPUT: 6V NiMH oder LiPo+6VBEC
5V LDO
3.3V LDO
Servo
BATT
STM32
MPU6050
Power Input
Servos
PCA9685 PWM Driver
Headers
5V Regulator

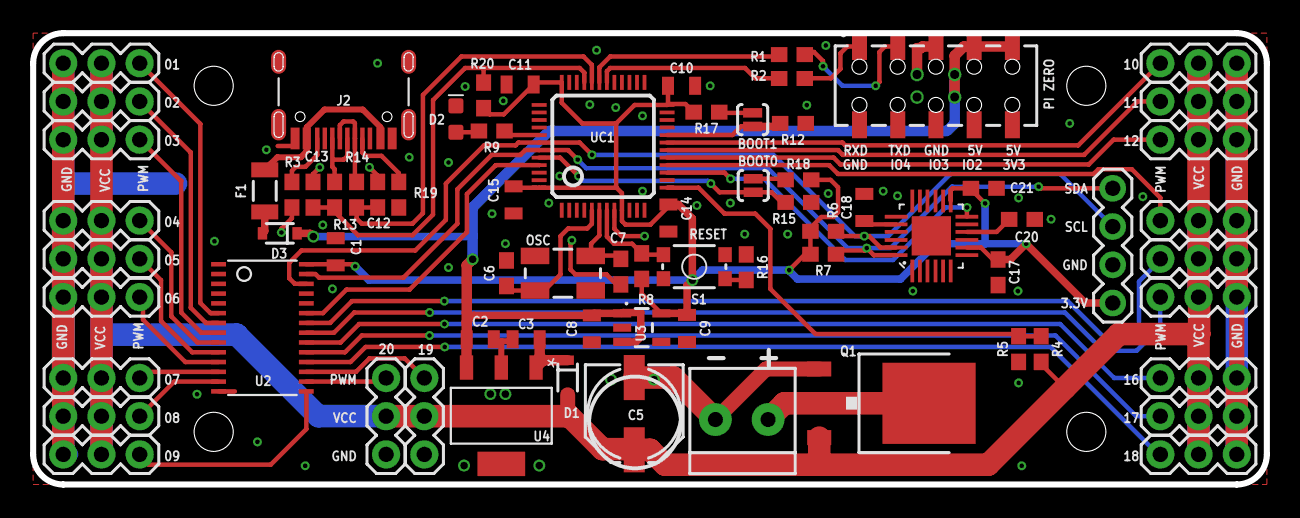
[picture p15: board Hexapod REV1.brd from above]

Board: 2 copper layers, 82.0 x 30.0 mm, 74 parts (0 on the bottom side), 55 nets.

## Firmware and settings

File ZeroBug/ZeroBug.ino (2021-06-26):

#include "ZeroBug.h"

#include <Adafruit_PWMServoDriver.h>
#include <Servo.h>

#define LED PB5
#define SDA1 PB7
#define SCL1 PB6
#define PCA_OE PB8

Adafruit_PWMServoDriver pwm = Adafruit_PWMServoDriver(0x40, Wire);

#define SERVOMIN  604.0 // This is the 'minimum' pulse length count (out of 4096)
#define SERVOMAX  2260.0 // This is the 'maximum' pulse length count (out of 4096)
#define SERVO_FREQ 50 // Analog servos run at ~50 Hz updates

Servo servo[4]; // local pwm servos

gaitEngine Hex;

byte tripodGait[120][6];
byte waveGait[120][6];

float jX = 0; // (Joystick) Walking X, Y and Rotate
float jY = 0.0;
float jR = 0.0;

long frameCounter = 0;

char inputBuffer[64]; // = "m 123.123 000.456 789.001";

float vBat = 0;

boolean IKError = false;

boolean powerup = false;
boolean powerdown = false;

boolean clawOpen = false;
boolean clawClose = false;
float clawPos = 0;

long controlTimeout;

void setup() {

  pinMode(LED, OUTPUT);
  pinMode(PCA_OE, OUTPUT);  
  digitalWrite(PCA_OE, HIGH);
  
  // tripod gait
  Hex.gaitSpeed = 1.0;
  Hex.legSpeed = 1.0;
  tripodGait[0][0]  = 1;
  tripodGait[0][2]  = 1;
  tripodGait[0][4]  = 1;
  
  tripodGait[30][1] = 1;
  tripodGait[30][3] = 1;
  tripodGait[30][5] = 1;
  
  tripodGait[60][0] = 1;
  tripodGait[60][2] = 1;
  tripodGait[60][4] = 1;
  
  tripodGait[90][1] = 1;
  tripodGait[90][3] = 1;
  tripodGait[90][5] = 1;
  
  
  // wave gait
  //Hex.gaitSpeed = 2.0;
  //Hex.legSpeed = 0.7;
  waveGait[00][0]  = 1;
  waveGait[20][4]  = 1;
  waveGait[40][2]  = 1;
  waveGait[60][5]  = 1;
  waveGait[80][1]  = 1;
  waveGait[100][3] = 1;
  
  memcpy(Hex.gSeq, tripodGait, sizeof(Hex.gSeq));
  
  Serial1.begin(115200);
  inputBuffer[0] = '\0'; //Initialize string to emtpy
  
  //Reset I2C bus
  pinMode(SDA1, OUTPUT);
  pinMode(SCL1, OUTPUT);
  digitalWrite(SDA1, HIGH);
  digitalWrite(SCL1, HIGH);
  delay(200);

  pwm.begin();
  pwm.setOscillatorFrequency(27000000);
  pwm.setPWMFreq(SERVO_FREQ);  // Analog servos run at ~50 Hz updates
  //Wire.setClock(400000);
  
  enableServos(true);
}

void loop() {

  if(controlTimeout < millis()) digitalWrite(LED, millis() % 200 <= 100);
  else digitalWrite(LED, millis() % 2000 <= 1000);
  

  if(powerup){
    if(Hex.traZ > 0){
      Hex.legS[0].setto(-70, -85, 0);
      Hex.legS[1].setto(-90, 0, 0);
      Hex.legS[2].setto(-70, 85, 0);
      Hex.legS[3].setto(70, 85, 0);
      Hex.legS[4].setto(90, 0, 0);
      Hex.legS[5].setto(70, -85, 0);
      Hex.traZ -= 0.3;
    }
    else{      
      powerup = false;
    }
  }
  else if(powerdown){
    if(Hex.traZ < 26){
      Hex.legS[0].setto(-65, -70, 0);
      Hex.legS[1].setto(-80, 0, 0);
      Hex.legS[2].setto(-65, 70, 0);
      Hex.legS[3].setto(65, 70, 0);
      Hex.legS[4].setto(80, 0, 0);
      Hex.legS[5].setto(65, -70, 0);
      Hex.traZ += 0.3;
    }
    else{
     powerdown = false;
    }
  }

  clawPos = constrain(clawPos, 0, 67);
  if(clawOpen){
    if(clawPos > 0) clawPos -= 2;
    else clawOpen = false;
  }
  else if(clawClose){
    if(clawPos < 58) clawPos += 2;
    else clawClose = false;
  }

  //stop hexapod if there is no connection from Raspi
  if(controlTimeout < millis()) {
    jX = 0;
    jY = 0;
    jR = 0;
  }
    
  // Configure and run the hexapod engine  
  Hex.walkX = jX;
  Hex.walkY = jY;
  Hex.walkR = jR;
  // Check for error in previous loop
  if(IKError){
    jX = 0;
    jY = 0;
    jR = 0;
  }  
  Hex.gaitStep();
  Hex.runBodyIK();
  IKError = (Hex.runLegIK() != 0);
  
  /*
  float angleA = 0;
  float angleB = 0;
  float angleC = 0;
  float angleD = 0;
  float angleE = 0;
  float angleF = 0;
  float angleG = 0;
  float angleH = 0;
  float angleI = 0;
  
  float angleJ = 0;
  float angleK = 0;
  float angleL = 0;
  float angleM = 0;
  float angleN = 0;
  float angleO = 0;
  float angleP = 0;
  float angleQ = 0;
  float angleR = 0;
  */
  
  float angleA = constrain( Hex.legAngle[0][0]*180/PI, -65, 65);
  float angleB = constrain(-Hex.legAngle[0][1]*180/PI, -100, 100);
  float angleC = constrain( Hex.legAngle[0][2]*180/PI, -100, 100);
  float angleD = constrain( Hex.legAngle[1][0]*180/PI, -65, 65);
  float angleE = constrain(-Hex.legAngle[1][1]*180/PI, -100, 100);
  float angleF = constrain( Hex.legAngle[1][2]*180/PI, -100, 100);
  float angleG = constrain( Hex.legAngle[2][0]*180/PI, -65, 65);
  float angleH = constrain(-Hex.legAngle[2][1]*180/PI, -100, 100);
  float angleI = constrain( Hex.legAngle[2][2]*180/PI, -100, 100);
  
  float angleJ = constrain( Hex.legAngle[3][0]*180/PI, -65, 65);  
  float angleK = constrain( Hex.legAngle[3][1]*180/PI, -100, 100);
  float angleL = constrain(-Hex.legAngle[3][2]*180/PI, -100, 100);
  float angleM = constrain( Hex.legAngle[4][0]*180/PI, -65, 65);
  float angleN = constrain( Hex.legAngle[4][1]*180/PI, -100, 100);
  float angleO = constrain(-Hex.legAngle[4][2]*180/PI, -100, 100);
  float angleP = constrain( Hex.legAngle[5][0]*180/PI, -65, 65);
  float angleQ = constrain( Hex.legAngle[5][1]*180/PI, -100, 100);
  float angleR = constrain(-Hex.legAngle[5][2]*180/PI, -100, 100);
  
  float angleS = constrain(Hex.rotZ*180/PI*1.7, -65, 65);
  float angleT = constrain(clawPos, 0, 67);

  angleA += -24;
  angleB += 18;
  angleC += 3;
  
  angleD += 14;
  angleE += 2;
  angleF += 0;
  
  angleG += 50;
  angleH += -12;
  angleI += -1;

  //---
  
  angleJ += -35;
  angleK += 11;
  angleL += 6;
  
  angleM += 3;
  angleN += 12;
  angleO += -6;

  angleP += 23;
  angleQ += 0;
  angleR += 0;

  angleS += -8;
  angleT += 0;

  
  int servoVALA = map(angleA*1000, -90*1000, 90*1000, SERVOMIN*1000, SERVOMAX*1000)/1000.0;
  int servoVALB = map(angleB*1000, -100*1000, 100*1000, SERVOMIN*1000, SERVOMAX*1000)/1000.0;
  int servoVALC = map(angleC*1000, -90*1000, 90 *1000, SERVOMIN*1000, SERVOMAX*1000)/1000.0;
  int servoVALD = map(angleD*1000, -90*1000, 90*1000, SERVOMIN*1000, SERVOMAX*1000)/1000.0;
  int servoVALE = map(angleE*1000, -100*1000, 100*1000, SERVOMIN*1000, SERVOMAX*1000)/1000.0;
  int servoVALF = map(angleF*1000, -90*1000, 90 *1000, SERVOMIN*1000, SERVOMAX*1000)/1000.0;
  int servoVALG = map(angleG*1000, -90*1000, 90*1000, SERVOMIN*1000, SERVOMAX*1000)/1000.0;
  int servoVALH = map(angleH*1000, -100*1000, 100*1000, SERVOMIN*1000, SERVOMAX*1000)/1000.0;
  int servoVALI = map(angleI*1000, -90*1000, 90 *1000, SERVOMIN*1000, SERVOMAX*1000)/1000.0;
  
  int servoVALJ = map(angleJ*1000, -90*1000, 90*1000, SERVOMIN*1000, SERVOMAX*1000)/1000.0;
  int servoVALK = map(angleK*1000, -100*1000, 100*1000, SERVOMIN*1000, SERVOMAX*1000)/1000.0;
  int servoVALL = map(angleL*1000, -90*1000, 90 *1000, SERVOMIN*1000, SERVOMAX*1000)/1000.0;
  int servoVALM = map(angleM*1000, -90*1000, 90*1000, SERVOMIN*1000, SERVOMAX*1000)/1000.0;
  int servoVALN = map(angleN*1000, -100*1000, 100*1000, SERVOMIN*1000, SERVOMAX*1000)/1000.0;
  int servoVALO = map(angleO*1000, -90*1000, 90 *1000, SERVOMIN*1000, SERVOMAX*1000)/1000.0;
  int servoVALP = map(angleP*1000, -90*1000, 90*1000, SERVOMIN*1000, SERVOMAX*1000)/1000.0;
  int servoVALQ = map(angleQ*1000, -100*1000, 100*1000, SERVOMIN*1000, SERVOMAX*1000)/1000.0;
  int servoVALR = map(angleR*1000, -90*1000, 90 *1000, SERVOMIN*1000, SERVOMAX*1000)/1000.0;

  int servoVALS = map(angleS*1000, -90*1000, 90 *1000, SERVOMIN*1000, SERVOMAX*1000)/1000.0;
  int servoVALT = map(angleT*1000, -90*1000, 90 *1000, SERVOMIN*1000, SERVOMAX*1000)/1000.0;
    
  static int testVal = SERVOMIN;
  if(testVal >= SERVOMAX) testVal = SERVOMIN;

  vBat = (float(analogRead(PA3))/4069.0)*10.321; // 4.7K+10K voltage divider

  batteryCheck();
    
  if(IKError){
    Serial.println("IKError Occured");
  }  
  else {
    pwm.writeMicroseconds(0, servoVALM);
    pwm.writeMicroseconds(1, servoVALN);
    pwm.writeMicroseconds(2, servoVALO);
    
    pwm.writeMicroseconds(3, servoVALP);  
    pwm.writeMicroseconds(4, servoVALQ);
    pwm.writeMicroseconds(5, servoVALR);
    
    pwm.writeMicroseconds(6, servoVALA);
    pwm.writeMicroseconds(7, servoVALB);
    pwm.writeMicroseconds(8, servoVALC); 

    servo[0].writeMicroseconds(servoVALD);
    servo[1].writeMicroseconds(servoVALE);
    servo[2].writeMicroseconds(servoVALF);
    
    servo[3].writeMicroseconds(servoVALJ);
    pwm.writeMicroseconds(15, servoVALK);    
    pwm.writeMicroseconds(14, servoVALL);
    
    pwm.writeMicroseconds(13, servoVALG);
    pwm.writeMicroseconds(12, servoVALH);  
    pwm.writeMicroseconds(11, servoVALI);   

    pwm.writeMicroseconds(10, servoVALS);
    pwm.writeMicroseconds(9, servoVALT);   
  }
  
  while (Serial1.available()>0){
    char input = Serial1.read();
    static int s_len; // static variables default to 0    
    if ((s_len >= 64) || (input != '\n' && input != '\r')) {
      inputBuffer[s_len++] = input;
    } else {      
      char commandChar = inputBuffer[0];      
      char * strtokIndx; // this is used by strtok() as an index
      strtokIndx = strtok(inputBuffer, " ");
      strtokIndx = strtok(NULL, " ");
      if(commandChar == 'm'){ // MOVE
        jX = atof(strtokIndx);
        strtokIndx = strtok(NULL, " ");
        jY = atof(strtokIndx);
        strtokIndx = strtok(NULL, " ");
        jR = atof(strtokIndx);
      }
      else if(commandChar == 't'){ // TRANSLATE
        Hex.traX = atof(strtokIndx);
        strtokIndx = strtok(NULL, " ");
        Hex.traY = atof(strtokIndx);
        strtokIndx = strtok(NULL, " ");
        Hex.traZ += atof(strtokIndx); // vorsicht!!! rückgängig machen?
      }
      else if(commandChar == 'r'){ // ROTATE
        Hex.rotX = atof(strtokIndx);
        strtokIndx = strtok(NULL, " ");
        Hex.rotY = atof(strtokIndx);
        strtokIndx = strtok(NULL, " ");
        Hex.rotZ = atof(strtokIndx);
      }
      else if(commandChar == 'u'){ // UP
        powerup = true;
      }
      else if(commandChar == 'd'){ // DOWN
        powerdown = true;
      }
      else if(commandChar == 'a'){ // Tripod Gait
        Hex.gaitSpeed = 1.0;
        Hex.legSpeed = 1.0;
        memcpy(Hex.gSeq, tripodGait, sizeof(Hex.gSeq));
      }
      else if(commandChar == 'b'){ // Wave Gait
        Hex.gaitSpeed = 2.0;
        Hex.legSpeed = 1.3;
        memcpy(Hex.gSeq, waveGait, sizeof(Hex.gSeq));
      }
      else if(commandChar == 'c'){ // CLOSE
        clawClose = true;
      }
      else if(commandChar == 'o'){ // OPEN
        clawOpen = true;
      }
      else if(commandChar == 'g'){ // CLAW fine adjust
        clawPos += atof(strtokIndx);
      }
      else if(commandChar == 'h'){ // heartbeat
        controlTimeout = millis()+3000;
      }
      // Reset buffer
      memset(inputBuffer, 0, sizeof(inputBuffer));
      s_len = 0;      
    }
  }
  
  while (Serial.available()>0){
    char input = Serial.read();
    static int s_len; // static variables default to 0    
    if ((s_len >= 64) || (input != '\n' && input != '\r')) {
      inputBuffer[s_len++] = input;
    } else {      
      char commandChar = inputBuffer[0];      
      char * strtokIndx; // this is used by strtok() as an index
      strtokIndx = strtok(inputBuffer, " ");
      strtokIndx = strtok(NULL, " ");
      if(commandChar == 'm'){ // MOVE
        jX = atof(strtokIndx);
        strtokIndx = strtok(NULL, " ");
        jY = atof(strtokIndx);
        strtokIndx = strtok(NULL, " ");
        jR = atof(strtokIndx);
      }
      else if(commandChar == 't'){ // TRANSLATE
        Hex.traX = atof(strtokIndx);
        strtokIndx = strtok(NULL, " ");
        Hex.traY = atof(strtokIndx);
        strtokIndx = strtok(NULL, " ");
        Hex.traZ = atof(strtokIndx);
      }
      else if(commandChar == 'r'){ // ROTATE
        Hex.rotX = atof(strtokIndx);
        strtokIndx = strtok(NULL, " ");
        Hex.rotY = atof(strtokIndx);
        strtokIndx = strtok(NULL, " ");
        Hex.rotZ = atof(strtokIndx);
      }
      else if(commandChar == 'u'){ // UP
        powerup = true;
      }
      else if(commandChar == 'd'){ // DOWN
        powerdown = true;
      }
      else if(commandChar == 'a'){ // Tripod Gait
        Hex.gaitSpeed = 1.0;
        Hex.legSpeed = 1.0;
        memcpy(Hex.gSeq, tripodGait, sizeof(Hex.gSeq));
      }
      else if(commandChar == 'b'){ // Wave Gait
        Hex.gaitSpeed = 2.0;
        Hex.legSpeed = 1.3;
        memcpy(Hex.gSeq, waveGait, sizeof(Hex.gSeq));
      }
      else if(commandChar == 'c'){ // CLOSE
        clawClose = true;
      }
      else if(commandChar == 'o'){ // OPEN
        clawOpen = true;
      }
      else if(commandChar == 'g'){ // CLAW fine adjust
        clawPos += atof(strtokIndx);
      }
      // Reset buffer
      memset(inputBuffer, 0, sizeof(inputBuffer));
      s_len = 0;      
    }
  }
  
  telemetry();

  debugOutput();
  
  //delay(10);
}

void debugOutput(){
  Serial.print("DBG");
  Serial.print(" ");
  Serial.print(jX);
  Serial.print(" ");
  Serial.print(jY);
  Serial.print(" ");
  Serial.print(jR);
  for(int i=0; i < 6; i++){
    Serial.print(" ");
    Serial.print(Hex.legAngle[i][0], 2);
    Serial.print(" ");
    Serial.print(Hex.legAngle[i][1], 2);
    Serial.print(" ");
    Serial.print(Hex.legAngle[i][2], 2);
  }
  Serial.print(" ");
  frameCounter = micros() - frameCounter;
  Serial.print(frameCounter/1000.0);
  Serial.print("ms ");  
  Serial.print(vBat);
  Serial.println("V");
  frameCounter = micros();
    
}

void telemetry(){
  static int cycleTimer = 0;
  if(cycleTimer++ > 40){
    Serial1.print("v ");
    Serial1.print(vBat);
    Serial1.print("\n");
    cycleTimer = 0;
  }  
}

// Disable servos if voltage is too low
void batteryCheck(){
  static int batteryTimer = 0;
  if(vBat < 5){
    if(batteryTimer > 50){
      enableServos(false);
    }
    batteryTimer++;
  }
  else if(vBat > 6){
    enableServos(true);
    batteryTimer = 0;
  }
}

void enableServos(boolean servOn){
  static boolean servosEnabled = false;
  if(!servosEnabled && servOn){
    digitalWrite(PCA_OE, LOW);
    servo[0].attach(PB1, SERVOMIN, SERVOMAX);
    servo[1].attach(PB0, SERVOMIN, SERVOMAX);
    servo[2].attach(PA7, SERVOMIN, SERVOMAX);
    servo[3].attach(PA6, SERVOMIN, SERVOMAX);
    servosEnabled = true;
  }
  else if(servosEnabled && !servOn){
    digitalWrite(PCA_OE, HIGH);
    servo[0].detach();
    servo[1].detach();
    servo[2].detach();
    servo[3].detach();
    servosEnabled = false;
  }
}

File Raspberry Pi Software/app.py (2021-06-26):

from aiohttp import web
import socketio
import asyncio
from gpiozero import CPUTemperature
import serial
import pygame
import os

sio = socketio.AsyncServer()
app = web.Application()
sio.attach(app)
loop = asyncio.get_event_loop()
pygame.display.init()



ser = serial.Serial(
    port='/dev/ttyS0', #Replace ttyS0 with ttyAM0 for Pi1,Pi2,Pi0
    baudrate = 115200,
    parity=serial.PARITY_NONE,
    stopbits=serial.STOPBITS_ONE,
    bytesize=serial.EIGHTBITS,
    timeout=0.01
)

async def serLoop():
    line = []
    while True:
        await asyncio.sleep(0.2)
        for c in ser.read():
            line.append(chr(int(c)))
            if chr(int(c)) == '\n':
                strSeg = ''.join(line).replace("\n", "")
                strSeg = strSeg.split(" ")
                if(len(strSeg) > 0):
                    if(strSeg[0] == 'v'):
                        await sio.emit('volt', float(strSeg[1]))
                line = []
                break

async def gameLoop():
    while True:
        try:
            pygame.joystick.init()
            # Check if there is a joystick
            if(pygame.joystick.get_count()) < 1:   
                pygame.joystick.quit()
                await asyncio.sleep(1) 
            else:   
                joystick = pygame.joystick.Joystick(0)
                break
        except pygame.error:
            pygame.joystick.quit()
            await asyncio.sleep(1) 
    while True:       
        try:
            await asyncio.sleep(0.01)
            joystick.init()

            if joystick.get_button(6):
                ser.write(('g 1\n').encode('utf-8'))
            if joystick.get_button(7):
                ser.write(('g -1\n').encode('utf-8'))
            if joystick.get_hat(0)[1] == 1:
                ser.write(('t 0 0 -0.3\n').encode('utf-8'))
            if joystick.get_hat(0)[1] == -1:
                ser.write(('t 0 0 0.3\n').encode('utf-8'))
                
            # Check for events
            for event in pygame.event.get():
                if event.type == pygame.JOYBUTTONDOWN:	
                    if joystick.get_button(3):
                        ser.write(('d\n').encode('utf-8'))
                    elif joystick.get_button(4):
                        ser.write(('u\n').encode('utf-8'))
                    elif joystick.get_button(15):
                        ser.write(('a\n').encode('utf-8'))
                    elif joystick.get_button(11):
                        ser.write(('b\n').encode('utf-8'))
                    elif joystick.get_button(0):
                        ser.write(('c\n').encode('utf-8'))
                    elif joystick.get_button(1):
                        ser.write(('o\n').encode('utf-8'))
                    elif joystick.get_button(13):
                        ser.write(('s\n').encode('utf-8'))
                if event.type == pygame.JOYAXISMOTION:                        
                    axis0 = joystick.get_axis(0)
                    axis1 = joystick.get_axis(1)
                    axis2 = joystick.get_axis(2)
                    axis3 = joystick.get_axis(3)
                    axis4 = (joystick.get_axis(4) -joystick.get_axis(5))/2

                    msxString = "{:7.3f}".format(axis0*0.7)
                    msyString = "{:7.3f}".format(-axis1*1.2)
                    msrString = "{:7.3f}".format(axis4*0.8)
                    yawString = "{:7.3f}".format(axis2/5)
                    pitchString = "{:7.3f}".format(axis3/4)
                    #print('m %s %s %s\n'%(msxString,msyString,msrString))
                    if joystick.get_button(6):
                        ser.write(('t %s %s 0\n'%("{:7.3f}".format(-axis0*20), "{:7.3f}".format(-axis1*32))).encode('utf-8'))
                    else:
                        ser.write(('m %s %s %s\n'%(msxString, msyString, msrString)).encode('utf-8'))
                    ser.write(('r 0 %s %s\n'%(pitchString, yawString)).encode('utf-8'))
                # Multiple events are generated for the same axis motion, so break after the first
                break
        except pygame.error:
            await asyncio.sleep(1) 

loop = asyncio.get_event_loop()
loop.create_task(gameLoop())
serialLoop = asyncio.get_event_loop()
serialLoop.create_task(serLoop())

def index(request):
    with open(os.path.dirname(__file__)+'/index.html') as f:
        return web.Response(text=f.read(), content_type='text/html')

async def sendTemp():
    while True:
        await asyncio.sleep(3)
        await sio.emit('temp', CPUTemperature().temperature)

loop.create_task(sendTemp())

async def heartbeat():
    while True:
        ser.write(('h\n').encode('utf-8'))
        await asyncio.sleep(1)

loop.create_task(heartbeat())

@sio.on('connect')
def chat_connection(sid, message):
    print('---- connected ----')
    
    
@sio.on('disconnect')
def chat_disconnect(sid):
    print('---- disconnected ----')

@sio.on('mov')
async def position(sid, msx, msy, msr):
    msxString = "{:7.3f}".format(float(msx))
    msyString = "{:7.3f}".format(float(-msy))
    msrString = "{:7.3f}".format(float(msr))
    #print('m %s %s %s\n'%("000.000",msyString,msrString))
    ser.write(('m %s %s %s\n'%(msxString,msyString,msrString)).encode('utf-8'))
    await asyncio.sleep(0.005)
    
@sio.on('rot')
async def position(sid, yaw, pitch, roll):
    yawString = "{:7.3f}".format(float(yaw/6))
    pitchString = "{:7.3f}".format(float(pitch/6))
    rollString = "{:7.3f}".format(float(roll/6))
    ser.write(('r %s %s %s\n'%(rollString, pitchString, yawString)).encode('utf-8'))
    await asyncio.sleep(0.005)

@sio.on('pos')
async def position(sid, message):
    if message == 1:
        ser.write(('u\n').encode('utf-8'))
    if message == 0:
        ser.write(('d\n').encode('utf-8'))
    await asyncio.sleep(0.005)
        
@sio.on('gait')
async def position(sid, message):
    if message == 1:
        ser.write(('a\n').encode('utf-8'))
    elif message == 0:
        ser.write(('b\n').encode('utf-8'))
    await asyncio.sleep(0.005)
    
@sio.on('claw')
async def position(sid, message):
    if message == 1:
        ser.write(('c\n').encode('utf-8'))
    elif message == 0:
        ser.write(('o\n').encode('utf-8'))
    await asyncio.sleep(0.005)

@sio.on('power')
async def position(sid, message):
    if message == 1:
        print('power down')

app.router.add_get('/', index)

if __name__ == '__main__':
    web.run_app(app, host='0.0.0.0', port=3000)
    loop.run_forever()
    serialLoop.run_forever()
    

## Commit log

2021-08-18 BOM added
    [Hexapod REV1.csv]
2021-11-20 Camera Streaming
    added support for displaying a video stream in the web-UI
2024-06-13 production files added
    [bom.csv, designators.csv, positions.csv]

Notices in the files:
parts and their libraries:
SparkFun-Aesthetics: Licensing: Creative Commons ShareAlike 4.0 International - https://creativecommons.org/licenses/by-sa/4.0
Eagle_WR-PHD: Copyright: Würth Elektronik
